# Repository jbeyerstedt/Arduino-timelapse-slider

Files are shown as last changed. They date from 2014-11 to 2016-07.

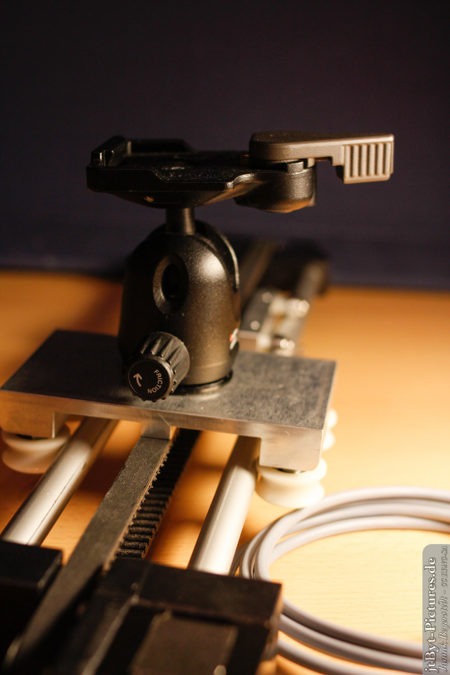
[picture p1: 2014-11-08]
additional files/Slider_Bilder-008.JPG

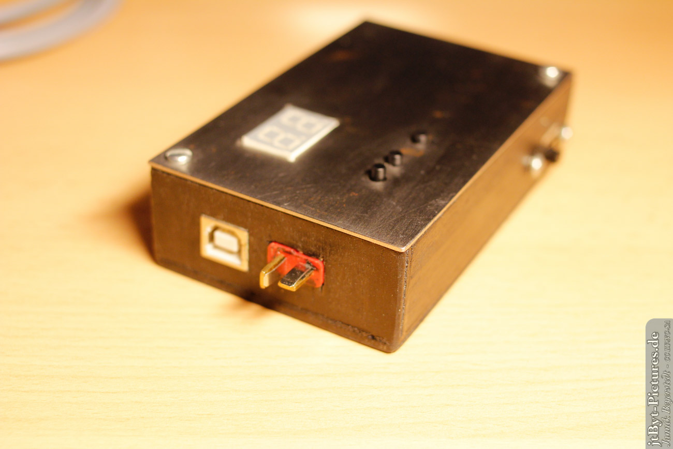
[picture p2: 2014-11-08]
additional files/Slider_Bilder-011.JPG

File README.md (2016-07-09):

# Arduino - timelapse-slider
by Jannik Beyerstedt from Hamburg, Germany  
[jannikbeyerstedt.de](http://jannikbeyerstedt.de) | [Github](https://github.com/jbeyerstedt)  
**license:** GNU GPL v3

## Software Documentation
This readme contains the introduction of the project, changelog and the **user manual** for the code/ software. Check also the "hardware_readme.md" and "electronics_readme.md".

## Introduction
I'm beginning shooting time lapses with my DSLR camera and wanted to have a slider for more interesting camera movements in my time lapses. So I began to write some code for the Arduino UNO board to control a stepper motor and the trigger of my camera.
To control this little thing I will use three buttons and two 7 digit displays.

You can find photos I made and in the future also videos on my website [jannikbeyerstedt.de](https://jannikbeyerstedt.de/fotografie).

## User Manual  
#### general information
1. the total slide time influences the sliding speed!

#### step by step guide
1. switch on power
2. The software initializes
	1. give it the starting point (left or right)
3. choose mode: interval trigger (**in**terval), timelapse slide (**sl**ide), movie (**co**ntinuous)
4. manual control (all modes the same)
	1. move carriage with plus and minus buttons
5. at interval trigger mode (it´s an interval trigger only)
	1. set trigger interval
	2. set direction
	3. push enter to begin
	4. end with enter -> back to step 4
6. at timelapse slide mode (interval trigger and carriage movement)
	1. set total slide time
	2. set direction
	3. set trigger interval
	4. push enter to begin
	5. it´ll end if time is elapsed or endstop hit -> back to step 4
	6. or abort by clicking enter -> back to step 4
7. at movie mode (no trigger, only carriage movement)
	1. set total movement time
	2. set direction
	3. push enter to begin
	4. it´ll end if time is elapsed or endstop hit -> back to step 4
	5. or abort by clicking enter -> back to step 4
8. change mode by reconnecting power or resetting the arduino

Symbols:

- In -> interval mode
- SL -> slider mode
- co -> movie mode (continuous)
- dr -> set total time (drive)
- In -> set trigger interval
- ┌ ┐ -> moving carriage
- \[ \] -> triggering camera
- – –  -> waiting for next triggering (interval trigger mode only)
- . -> idle/ manual drive possible

## Setup Manual
This will explain the options that can be set in the config.h file. But it´s quite well commented in the file itself as well.  
more follows soon / mehr folgt bald  

## what should the software do?
#### in general
* input values: time to slide the whole slider, slide direction, trigger interval
* have a stop button to escape the slide
* trigger the camera
* stop the slide at triggering the camera
* tree buttons as inputs (plus, minus, enter)
* drive two 8-bit shift registers for the displays
* drive a stepper motor (via stepper motor driver IC)

#### additional in version 1.0
* movie mode with constant velocity
* (more or less) smart symbols on the display indicating the direction, current mode and errors

#### additional in version 2.0
* INFO: movie and interval mode are disabeled until ready in v2.1
* coded as finite state machine
* 3 modes for timelapse, timelapse with slider, movie
* virtual endstops
* steps are done in the background
	* faster stepping possible
	* more responsive exit from slide
* set initial carriage position
* remember last settings (start at last entered number for slideTime, etc.)
* better virtual endstop methods
* some extensive serial prints can be disabled
* functionality for pure interval triggering added 

#### additional in version 2.1
* functionality for movie mode

## Changelog
* 1.0.1:
	* setSlideTime=0 will get an division through 0 in the calculation which causes malfunction (because stepsPerInterval will be 0)
	* corrected the calculation of the stepsPerInterval at high speed / setSlideTime < 3 / calculated stepsPerSecond < than the highest possible speed
* 1.0.2:  
	* little modification at big slide times
* 2.0 beta1 :
	* INFO: movie and interval mode are disabeled until ready in v2.1
	* all new rewritten version. New software concept and it´s C++ now.
	* 3 modes for timelapse, timelapse with slider, movie
	* classes for:
		* the slider (carriage)
		* the stepper motort
		* the buttons
	* display.h restructured and enhanced:
		* "dynamic" calcualtion of the symbols
		* new function for symbols only
		* number function does ONLY numbers now
		* number function can do negative numbers up to -9
	* enter start position (for virtual endstops)
	* move carriage with plus and minus buttons (for position counting)
* 2.0.1:
	* remember last settings (start at last entered number for slideTime, etc.)
	* better virtual endstop methods
	* some extensive serial prints can be disabled
	* functionality for pure interval triggering added
	* several bugfixes
* 2.1.0:
	* movie mode added
	
* TODO:
	* add a state machine documentation

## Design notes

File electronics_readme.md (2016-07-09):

# Arduino - timelapse-slider
by Jannik Beyerstedt from Hamburg, Germany  
[jannikbeyerstedt.de](http://jannikbeyerstedt.de) | [Github](https://github.com/jbeyerstedt)  
**license:** GNU GPL v3

## Electronics Documentation
This document describes the electronics part of the Arduino timelapse slider, but it will not be a complete instuction to rebuild everything I made. It´s more like all the parts you´ll need to build it, but there is enough you must do by yourself. I can´t explain every wire I used.  
Kepp in mind, that your camera may be triggered in a different way. Canon DSLRs are easy. You only must connect two pins of the remote connector. Some cameras are using different resistors to detect focus and trigger. Please ask google to find out more about your camera.

## parts I used:

amount | description  
--	| ---  
1	| Arduino Uno Rev3
1	| A4988 Stepper Motor Driver Carrier
2	| 8 bit shift registers
2	| 7 segment display (+ resistors)
1	| miniature relais (to trigger my Canon DSLR)
3	| miniature buttons
1	| T-connector (used at LiPo-batteries) for power supply

*	dot matrix circuit boards
*	pins to connect to the arduino
*	DIN-connectors for the wires to camera and motor
*	jumpers for different modes of the stepper motor driver
*	small wires with different colors to connect everything

**weblinks**

*	stepper motor driver: [http://www.exp-tech.de/Shields/A4988-Stepper-Motor-Driver-Carrier.html]()
*	stepper motor [http://www.exp-tech.de/Servos-und-Motoren/Stepper-Motor-Bipolar-200-Steps-Rev-35x36mm-2-7V-1000mA.html]()

## installation notes :
##### english:
###### display

*	you can drive one seven-segment-display each with one 8-bit shift register and you can connect two shift registers at one output of your arduino (but you will need tree pins for clock, latch and data)
*	connect each output of your shift register to one segment of the display with an restistor between them. Keep in mind, whether the display is collected kathode or anode and whether you can get positive or negative voltage from your shift register.
*	driving a shift register with an arduino is explained at the arduino website.
*	If you use my code copy and paste, than you have to check whether everything is connected to the same pin I used. Otherwise you must change the constants at the beginning of the code.

###### stepper motor

*	connect the stepper motor driver your arduino, an power supply and your stepper motor. Do never switch the driver on without an stepper motor (see manual of the driver).
*	read the manual and try the driver with a code snippet. If that works, you can put that code in your project.
*	If you use my code copy and paste, than you have to check whether everything is connected to the same pin I used. Otherwise you must change the constants at the beginning of the code.

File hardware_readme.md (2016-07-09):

# Arduino-Timelapse-Slider
# Arduino - timelapse-slider
by Jannik Beyerstedt from Hamburg, Germany  
[jannikbeyerstedt.de](http://jannikbeyerstedt.de) | [Github](https://github.com/jbeyerstedt)  
**license:** GNU GPL v3

## Hardware Documentation 
This is the documentation for the technical drawings and all the hardware.
all the technical drawings are specific to the parts I used. If you use other parts, some measurements must be changed.  

## basic Measurements

* distance between the tubes (inner edges): 45 mm
* tubes diameter: 12 mm
* bearings: 10mm x 4 mm

## parts I used

amount | description  
--	| ---  
12	| ball bearings MR 104 ZZ / 4 x 10 x 4 mm  
8	| zylindrical head screws M4x15  
4	| zylindrical head screws M4x20  
24	| nuts M4 (8 as distance roll, 16 as counter nut and for the correct distance)  
4	| rope reel with ball bearings (detailed information see weblink section) <br> outer diameter 24 mm, inner diameter 20 mm, height 11 mm  
4	| screws M5x15  
4	| nuts M5 (as counter nut and distance roll)  
1	| M5 screw and washer to fasten the quick release plate
1	| manfrotto 200PL quick release plate
1	| manfrotto ball head (using the 1/4 zoll screw of the QR-plate to fasten it)
1 m | toothed belt 5M-9 
2 	| toothed disk (gear) 12-5M-9 
4	| tiny M3 screws to secure the belt
1	| stepper motor (bipolar, 2.7V, 1000mA) by pololu

*	small screws to fasten the stepper motor

**weblinks**  

*	rope reel: [http://jost-technik.de/Klappensteller/Zubehoer---Sonstiges/Umlenkrolle-fuer-Huehnerklappe.html]()
*	ball brearings from ebay
*	toothed belt and disk: [https://zahnriemen24.de]()
*	stepper motor [http://www.exp-tech.de/Servos-und-Motoren/Stepper-Motor-Bipolar-200-Steps-Rev-35x36mm-2-7V-1000mA.html]()

## installation notes:
##### english:
###### tubes, tube support and stepper motor
*	build one tube support, that holds the two tubes and a gear for the belt
*	build another tube support, that can hold the stepper motor with the other gear on it.

###### inner sledge
*	the inner sledge uses the 10 mm bearings to be held in position. On every side (left and right) are 2 bearings at the top, 2 at the bottom and two on the inner side. All of them are on M4-Screws.
* 	the inner bearings have a nut on top and bottom as distance tubes, you can also use 3 mm thick tubes instead. The screw of these bearings is also used to hold the tree parts of the inner sledge together. They must be at least 15 mm long
* 	the outer bearings will be placed on the shorter M4 screws with two nut (each 3 mm) to hold them in place and keep them at the correct distance from the sledge.

###### outer sledge
*   put the rope reel on the M5 screw and secure with one nut. Screw it carefully to the aluminium base AND put it on the rails (tubes).

###### toothed belt
*	cut the belt in two pieces, drill a hole for the M3 screws betwen the tooths to one side of each belt
*	hold the belt on the slider to get the correct legth and mark the position for the screw. Kepp in mind, that the two belts will have different lenghts.
*	drill the other two holes
*	screw the belt to your slider

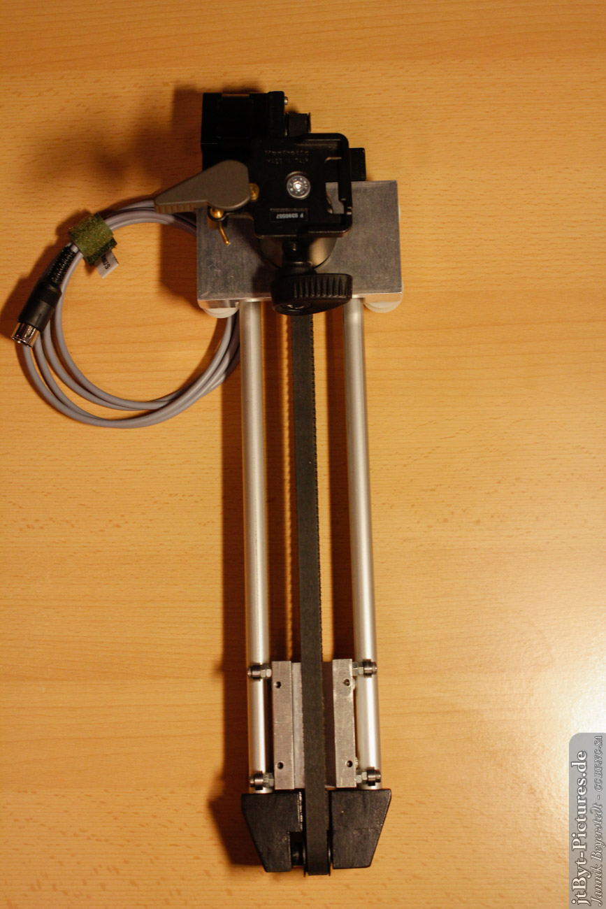
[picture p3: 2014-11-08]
additional files/Slider_Bilder-006.JPG

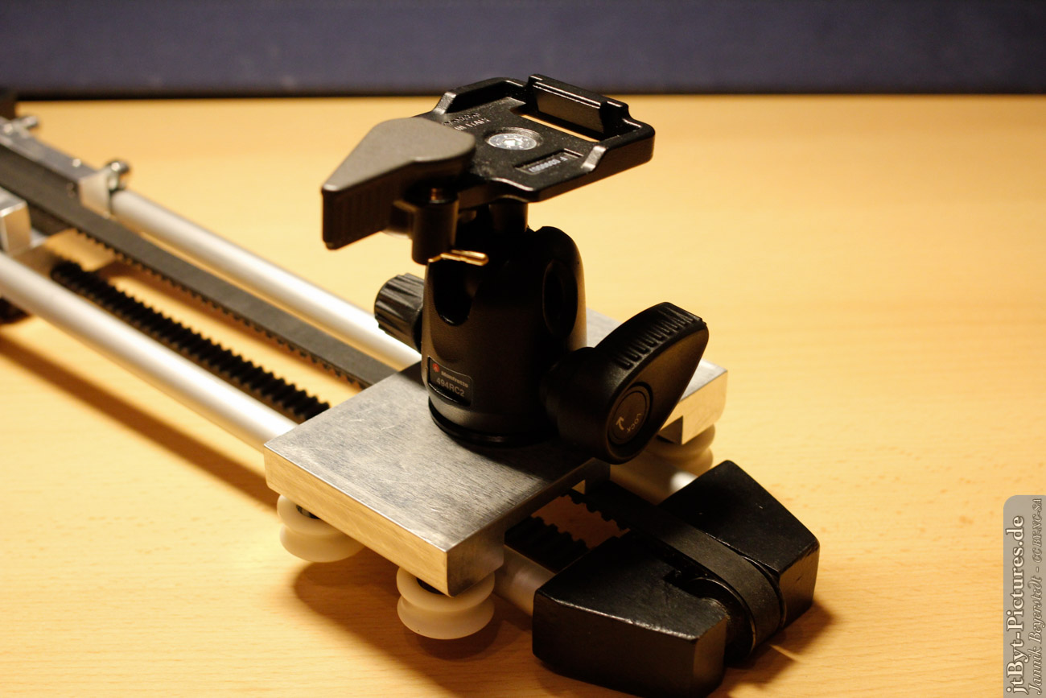
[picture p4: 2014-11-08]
additional files/Slider_Bilder-005.JPG

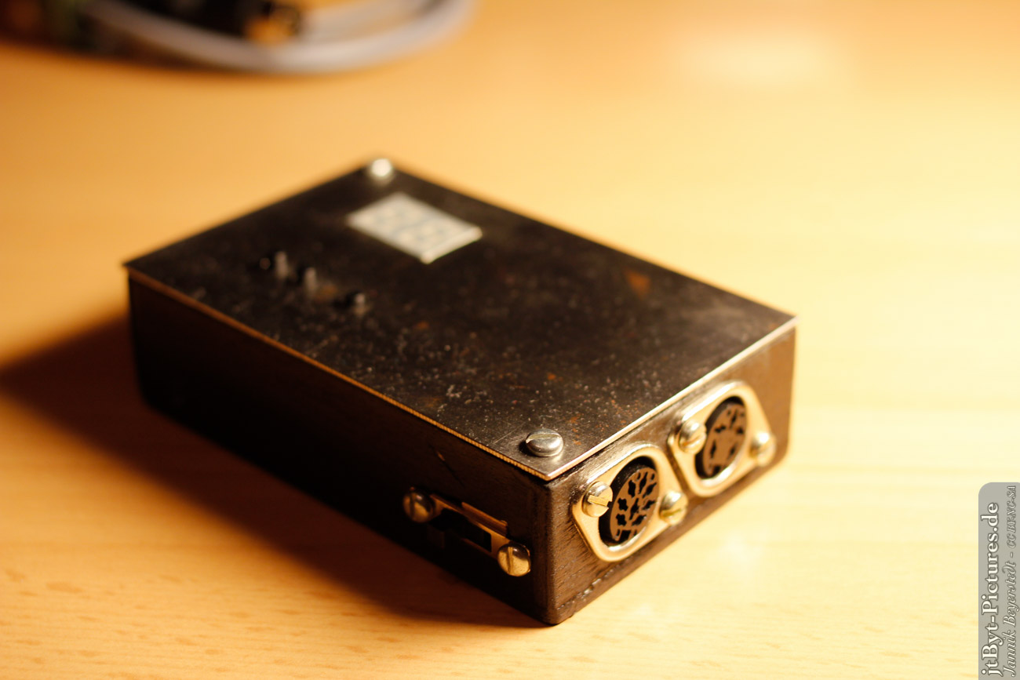
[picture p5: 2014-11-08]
additional files/Slider_Bilder-010.JPG

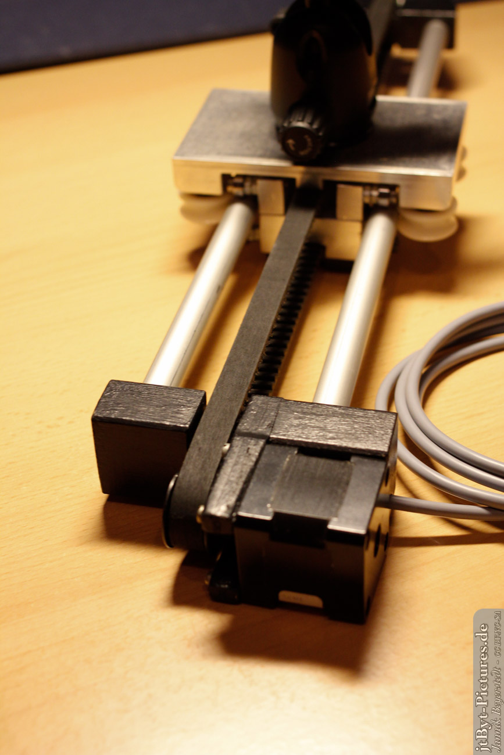
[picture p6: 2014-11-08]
additional files/Slider_Bilder-003.JPG

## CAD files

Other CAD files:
additional files/ArduinoSlider-Schlitten_Innen.dwg

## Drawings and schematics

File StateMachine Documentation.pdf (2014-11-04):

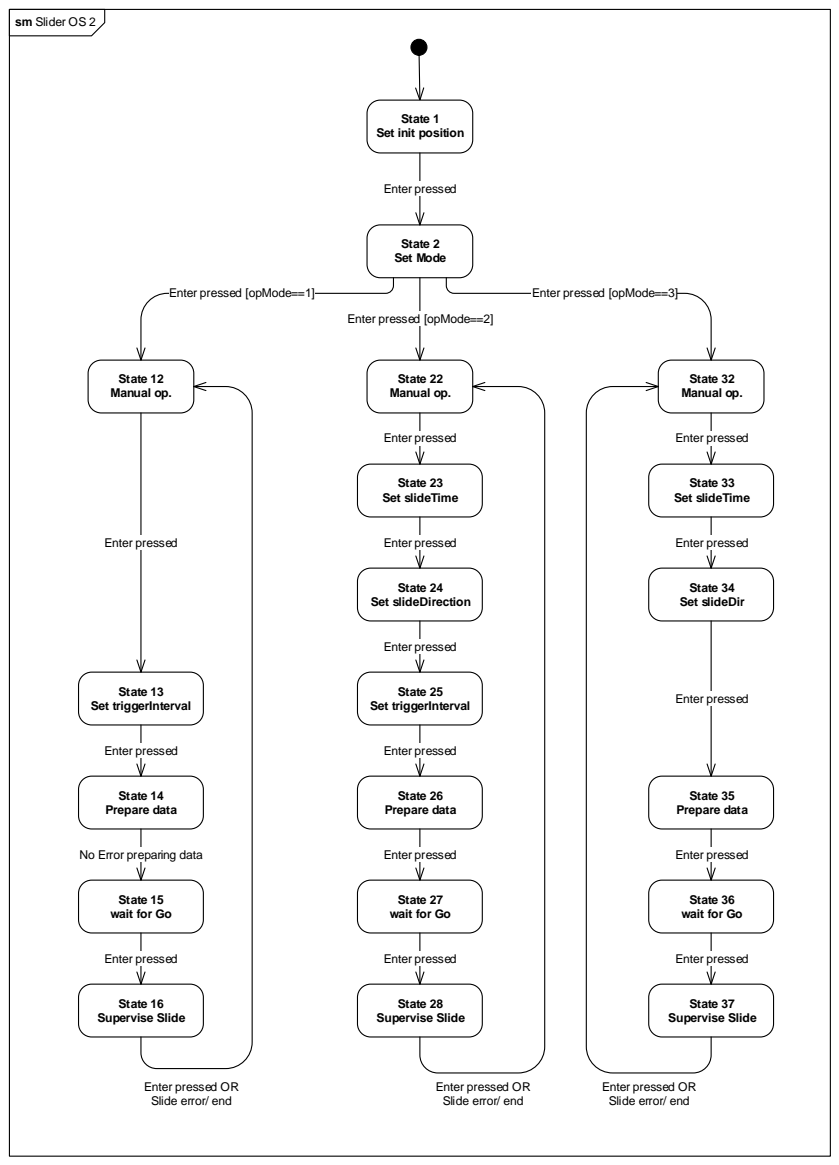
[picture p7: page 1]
State 12 Manual op.; State 22 Manual op.; State 32 Manual op.; State 2 Set Mode; Enter pressed; [opMode==2]; State 13 Set triggerInterval; State 23 Set slideTime; State 33 Set slideTime; State 24 Set slideDirection; State 34 Set slideDir; State 25 Set triggerInterval; State 14 Prepare data; State 35 Prepare data; State 26 Prepare data; No Error preparing data; State 16 Supervise Slide; State 28 Supervise Slide; State 37 Supervise Slide

sm Slider OS 2

State 1
Set init position

Enter pressed [opMode==1]

Enter pressed [opMode==3]

State 15
wait for Go

State 27

State 36

Enter pressed OR
Slide error/ end

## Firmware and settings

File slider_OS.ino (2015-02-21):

/*
 * project: slider OS 2
 * for controlling a timelapse slider and triggering the Camera
 * with an arduino, 3 buttons, 2 7-segment-displays, stepper driver
 *
 * for debouncing the buttons the Bounce2 library is used. Download it here:
 * https://github.com/thomasfredericks/Bounce-Arduino-Wiring
 * 
 * copyright: Jannik Beyerstedt | http://jannikbeyerstedt.de | code@jannikbeyerstedt.de
 * license: http://www.gnu.org/licenses/gpl-3.0.txt GPLv3 License
 *
 * version 2.1.1 (08.11.2014)
 * changelog: see readme.md
 */


#include <Bounce2.h>

#include "config.h"
#include "button.h"
#include "display.h"
#include "my_classes.h"
#include "slow_impulses.h"


int currentState = -1; 
int opMode  = 0;       // operation mode - 1: IN - 2: SL - 3: CO

int choosenNumber = 0;
boolean slideError = false;
int buttonsHelper = 0; // variable to temporarly store button return values
int buttonsLastVal = 0;

int slideTime = 1;
int slideDirection = 0; // 1 = right, 0 = left
int triggerInterval = 0;



ButtonPair buttons (buttonPlusPin, buttonMinusPin);
//Button buttonEnter (buttonEnterPin); // for a normally working button
Button2 buttonEnter (buttonEnterPin); // special for my broken button

SlowImpulses stepper;

Slider mySlider(&stepper);



void setup() {
  pinMode(ledPin, OUTPUT);
  pinMode(shiftLatch, OUTPUT);
  pinMode(shiftClock, OUTPUT);
  pinMode(shiftData, OUTPUT);
  
  pinMode(buttonPlusPin, INPUT);
  pinMode(buttonMinusPin, INPUT);
  pinMode(buttonEnterPin, INPUT);
  
  pinMode(stepperStep, OUTPUT);
  pinMode(stepperDir, OUTPUT);
  pinMode(stepperSleep, OUTPUT);
  
  pinMode(trigger, OUTPUT);
  
  digitalWrite(stepperSleep, LOW); // set stepper driver to sleep
  
  stepper.init(stepperStep);
  
  #ifndef NO_SERIAL_COM
  Serial.begin(9600);
  #endif
}


void loop() {
  
  // read all buttons
  buttons.update();
  buttonEnter.update();
  
  
  // do something based on the case
  switch (currentState) {
    
    case 1:  // initialize carriage position
      
      buttons.setInterval(0,2);
      buttonsHelper = buttons.getValue();  
      switch (buttonsHelper) {
        case 0: // left
          displaySymbol(initLeft);
          mySlider.initCarriagePosition(0);
          break;
        case 2: // right
          displaySymbol(initRigt);
          mySlider.initCarriagePosition(maxSteps);
          break;
        default:
          displaySymbol(initPos);
          break;
      }
      
      if (buttonEnter.triggered() ) {
        Serial.print("initial position: "); Serial.println(buttonsHelper);
        
        currentState = 2;
        #ifdef INFO_COM
        Serial.println("--switch to state 2");
        #endif
      }
      
      break;
    
    case 2:  // initialization / set mode
      buttons.setInterval(0,3);
      opMode = buttons.getValue();
      switch (opMode) {
        case 1: // IN
          displaySymbol(modeIn);
          break;
        case 2: // SL
          displaySymbol(modeSl);
          break;
        case 3: // CO
          displaySymbol(modeCo);
          break;
        default:
          displaySymbol(waitInput);
          break;
      }
      
      if (buttonEnter.triggered() ) {
        Serial.print("mode: "); Serial.println(opMode);
        switch (opMode) {
          case 1: // IN
            buttons.reset();
            buttons.setInterval(-maxSteps ,maxSteps, (1000/maxVelocity) ); // step interval = 1/maxVelocity in ms
            currentState = 12;
            #ifdef INFO_COM
            Serial.println("--switch to state 12");
            #endif
            break;
          case 2: // SL
            buttons.reset();
            buttons.setInterval(-maxSteps ,maxSteps, (1000/maxVelocity) ); // step interval = 1/maxVelocity in ms
            currentState = 22;
            #ifdef INFO_COM
            Serial.println("--switch to state 22");
            #endif
            break;
          case 3: // CO
            buttons.reset();
            buttons.setInterval(-maxSteps ,maxSteps, (1000/maxVelocity) ); // step interval = 1/maxVelocity in ms
            currentState = 32;
            #ifdef INFO_COM
            Serial.println("--switch to state 32");
            #endif
            break;
          default:
            displaySymbol(waitInput);
            Serial.println("ERROR: no mode set");
            break;
        }
      }
      
      break;
      
    case 12:  // manual operation / idle
    case 22:
    case 32:
      displaySymbol(waitIdle);
      
      buttonsHelper = buttons.getValue();
      
      digitalWrite(stepperSleep, HIGH);
      
      if (buttonsHelper > buttonsLastVal ) {        // right
        buttonsLastVal = buttonsHelper;
        mySlider.manualRight();
      }else if (buttonsHelper < buttonsLastVal ) {  // left
        buttonsLastVal = buttonsHelper;
        mySlider.manualLeft();
      }
      
      
      if (buttonEnter.triggered() ) {
        switch (opMode) {
          case 1: // IN
            buttons.setInterval(1,numberLimitTriggerTime);
            buttons.presetValue(triggerInterval); // preset last entered value
            
            displaySymbol(setInt); delay(500);
            currentState = 13;
            #ifdef INFO_COM
            Serial.println("--switch to state 13");
            #endif
            break;
          case 2: // SL
            buttons.setInterval(1,numberLimitSlideTime);
            buttons.presetValue(slideTime); // preset last entered value
            
            displaySymbol(setTime); delay(500);
            currentState = 23;
            #ifdef INFO_COM
            Serial.println("--switch to state 23");
            #endif
            break;
          case 3: // CO
            buttons.setInterval(1,numberLimitSlideTime);
            buttons.presetValue(slideTime); // preset last entered value
            
            displaySymbol(setTime); delay(500);
            currentState = 33;
            #ifdef INFO_COM
            Serial.println("--switch to state 33");
            #endif
            break;
          default:
            displaySymbol(waitInput);
            currentState = 0;
            Serial.println("ERROR: no mode set -> reset");
            break;
        }
      }
      break;  
    
    case 23:  // set total time
    case 33:
      slideTime = buttons.getValue();
      displayNumber(slideTime);
      
      if (buttonEnter.triggered() ) {
        Serial.print("slideTime: "); Serial.println(slideTime);
        switch (opMode) {
          case 2: // SL
            buttons.setInterval(0,1);
            buttons.presetValue(slideDirection); // preset last entered value
            currentState = 24;
            #ifdef INFO_COM
            Serial.println("--switch to state 24");
            #endif
            break;
          case 3: // CO
            buttons.setInterval(0,1);
            buttons.presetValue(slideDirection); // preset last entered value
            currentState = 34;
            #ifdef INFO_COM
            Serial.println("--switch to state 34");
            #endif
            break;
          default:
            displaySymbol(waitInput);
            currentState = 0;
            Serial.println("ERROR: no mode set -> reset");
            break;
        }
      }
      break;
    
    case 24:  // set carriage movement direction
    case 34:
      slideDirection = buttons.getValue();  
      if (slideDirection == 1) { // right
        displaySymbol(dirRigt);
      }else if (slideDirection == 0) { // left
        displaySymbol(dirLeft);
      }
      
      if (buttonEnter.triggered() ) {
        Serial.print("slideDirection: "); Serial.println(slideDirection);
        switch (opMode) {
          case 1: // IN
            buttons.reset();
            currentState = 15;
            #ifdef INFO_COM
            Serial.println("--switch to state 15");
            #endif
            break;
          case 2: // SL
            buttons.setInterval(1,numberLimitTriggerTime);
            buttons.presetValue(triggerInterval); // preset last entered value
            
            displaySymbol(setInt); delay(500);
            currentState = 25;
            #ifdef INFO_COM
            Serial.println("--switch to state 25");
            #endif
            break;
          case 3: // CO
            buttons.reset();
            currentState = 35;
            #ifdef INFO_COM
            Serial.println("--switch to state 35");
            #endif
            break;
          default:
            displaySymbol(waitInput);
            currentState = 0;
            Serial.println("ERROR: no mode set -> reset");
            break;
        }
      }
      break;
    
    case 13:  // set trigger interval
    case 25:
      triggerInterval = buttons.getValue();
      displayNumber(triggerInterval);
      
      if (buttonEnter.triggered() ) {
        Serial.print("triggerInterval: "); Serial.println(triggerInterval);
        switch (opMode) {
          case 1: // IN
            buttons.reset();
            currentState = 14;
            #ifdef INFO_COM
            Serial.println("--switch to state 14");
            #endif
            break;
          case 2: // SL
            buttons.reset();
            currentState = 26;
            #ifdef INFO_COM
            Serial.println("--switch to state 26");
            #endif
            break;
          default:
            displaySymbol(waitInput);
            currentState = 0;
            Serial.println("ERROR: no mode set -> reset");
            break;
        }
      }
      break;
    
    case 14:  // prepare data / set slide parameters
    case 26:
    case 35:
      #ifdef INFO_COM
      Serial.println("--data preparation");
      #endif
      displaySymbol(waitGo);
      
      switch (opMode) {
        case 1: // IN
          mySlider.setParameters(opMode, 0, triggerInterval, 0);
          
          buttons.reset();
          currentState = 15;
          #ifdef INFO_COM
          Serial.println("--switch to state 15");
          #endif
          break;
        case 2: // SL
          mySlider.setParameters(opMode, slideTime, triggerInterval, slideDirection);
          
          buttons.reset();
          currentState = 27;
          #ifdef INFO_COM
          Serial.println("--switch to state 27");
          #endif
          break;
        case 3: // CO
          mySlider.setParameters(opMode, slideTime, 0, slideDirection);
          
          buttons.reset();
          currentState = 36;
          #ifdef INFO_COM
          Serial.println("--switch to state 36");
          #endif
          break;
        default:
          displaySymbol(waitInput);
          currentState = 0;
          Serial.println("ERROR: no mode set -> reset");
          break;
      }
      break;
    
    case 15:  // wait for go
    case 27:
    case 36:
      
      if (buttonEnter.triggered() ) {
        switch (opMode) {
          case 1: // IN
            buttons.reset();
            mySlider.startSequence();
            currentState = 16;
            #ifdef INFO_COM
            Serial.println("--switch to state 16");
            #endif
            break;
          case 2: // SL
            buttons.reset();
            mySlider.startSequence();
            currentState = 28;
            #ifdef INFO_COM
            Serial.println("--switch to state 28");
            #endif
            break;
          case 3: // CO
            buttons.reset();
            mySlider.startSequence();
            currentState = 37;
            #ifdef INFO_COM
            Serial.println("--switch to state 37");
            #endif
            break;
          default:
            displaySymbol(waitInput);
            currentState = 0;
            Serial.println("ERROR: no mode set -> reset");
            break;
        }
      }
      break;
    
    case 16:  // supervise slide operation
    case 28:
    case 37:
                  
      if ( mySlider.update() ) {
        // normal operation
        slideError = false;
      }else {
        // virtual endstop hit
        slideError = true;
        displaySymbol(errorGen);
        delay(1000);
      }
      
      
      if (buttonEnter.triggered() || (slideError) ) {
        switch (opMode) {
          case 1: // IN
            mySlider.stopSequence();
            
            buttons.reset();
            buttons.setInterval(-maxSteps ,maxSteps, (1000/maxVelocity) ); // step interval = 1/maxVelocity in ms
            currentState = 12;
            #ifdef INFO_COM
            Serial.println("--switch to state 12");
            #endif
            break;
          case 2: // SL
            mySlider.stopSequence();
            
            buttons.reset();
            buttons.setInterval(-maxSteps ,maxSteps, (1000/maxVelocity) ); // step interval = 1/maxVelocity in ms
            currentState = 22;
            #ifdef INFO_COM
            Serial.println("--switch to state 22");
            #endif
            break;
          case 3: // CO
            mySlider.stopSequence();
            
            buttons.reset();
            buttons.setInterval(-maxSteps ,maxSteps, (1000/maxVelocity) ); // step interval = 1/maxVelocity in ms
            currentState = 22;
            #ifdef INFO_COM
            Serial.println("--switch to state 32");
            #endif
            break;
          default:
            displaySymbol(waitInput);
            currentState = 0;
            Serial.println("ERROR: no mode set -> reset");
            break;
        }
        
      }
      break;
    
    default:
      // initialise all systems
      // or something wrong happened
      Serial.println("--reset (default case)");
      currentState = 1;
      buttons.presetValue (1); // init position: display "initPos" first.
      
      break;
  } // end switch
  
  
} // end loop





// timer compare interrupt service routine
// must be in main file / can´t figure out how to do it in the impulse.h or impule.cpp
ISR(TIMER1_COMPA_vect)
{ 
  if (stepper.durationCount < stepper.durationCompare ) {
    stepper.durationCount++;
    digitalWrite(stepper.pinNo, digitalRead(stepper.pinNo) ^ 1);
  }else {
    stepper.durationStatus = false;
    stepper.stop();
  }
}

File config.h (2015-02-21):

/*
 * project: slider OS 2
 * file: config.h
 *
 * copyright: Jannik Beyerstedt | http://jannikbeyerstedt.de | code@jannikbeyerstedt.de
 * license: http://www.gnu.org/licenses/gpl-3.0.txt GPLv3 License
 *
 * version 2.1.1 (08.11.2014)
 */

/*
  configurations file
*/


#ifndef __config_h__
#define __config_h__
 
// basic config
// --------------------

// define input pins
#define trigger 2
//#define servoTilt 3

#define buttonPlusPin  A1
#define buttonMinusPin A2
#define buttonEnterPin A0

// define output pins
#define shiftLatch   12
#define shiftClock    9
#define shiftData     8
#define ledPin       13
#define stepperStep   6
#define stepperDir    7
#define stepperSleep  4

// set mechanical properties
const int triggerDuration = 500;   // how long should your camera be triggered (exposure time is still set in camera)
const int maxSteps        = 1740;  // amount of steps to slide the slider along {my calue for half step: 2200}
const int maxVelocity     = 50;    // maximum number of steps per second you stepper motor can perform
#define INVERT_STEPPER_DIR         // invert stepper direction, that it matches your buttons (right button, slide right)


// advanced config
// --------------------

// define the maximum number displayed
const int numberLimitSlideTime = 30;    // maximum time input to slide (in minutes)
const int numberLimitTriggerTime = 10;  // maximum trigger interval time (in seconds)

// define the number os milliseconds to retrigger a count-up if button is held down
const int fastCountInterval = 150;

//#define DEBUG_COM                 // enable detailed info (position values) (default: off)
//#define INFO_COM                  // enable info log (state changes) messages via serial 
//#define NO_SERIAL_COM             // disable all serial communication (default: off)

// debug config
// --------------------
const int debounceDelay = 20;
const int readThreshold = 900;


#endif

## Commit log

2013-06-08 various improvements
    changed symbols for indicating different states
    added the enter button as abort of the slide
2013-09-01 AutoCAD files of the inner slider sledge
    bad quality, i´ll do a better technical drawing of all machined parts
    in the future
    [ArduinoSlider-Schlitten_Innen.dwg]
2013-09-01 update to version 0.3
    now, that the pysical part of the slider is ready, I updated some
    values,
    added the trigger,
    corrected the slide direction
    added the calulation section
    [slider_OS.ino]
2013-09-01 new arduino sketch to test the setup without conversion
    like version 0.2
2013-09-01 update to 1.0.1 minor bugfixes - see new changelog
    fixed two bugs
    added changelog to the readme.md
    [slider_OS.ino]
2013-10-10 deleted AutoCAD files
    because they will not be completed. New drawings will follow soon.
    [ArduinoSlider-Schlitten_Innen.dwg]
2014-10-13 added another state for initialization of carriage
    changes for new Slider::setParameters
2014-10-13 experiments for driving stepper
    commit before changing to new branch, because it´s not working now.
    [my_classes.cpp]
2014-10-13 serious fix of problems with pointers
    pointer to the stepper instance was handled wrong
    [my_classes.cpp]
2014-10-13 init carriage position, housekeeping
    new state for initializing the carriage position
    plenty of housekeeping
2014-10-18 release version of buttons library
2014-10-19 v2.0 beta1
    new function for inverting stepper dir if necessary
    [config.h]
2014-10-21 little bugfix in manualLeft
    changed maximum frequency for manual operation to the maximum set in
    config.h
    [my_classes.cpp, slider_OS.ino]
2014-10-21 remember last set values
    therefore added ButtonPair::presetValue
2014-10-21 new positioning function for SL-mode
    + bugfix: forgot to make the changes of the last commit also on one
    other position
    [my_classes.cpp, slider_OS.ino]
2014-10-21 print some status info only for debug
2014-10-21 v2.0.1: functionality for interval trigger added
    + bugfixes
    + new error symbol
    + intervalTrigger class
    + some proper names
    [config.h, my_classes.cpp, slider_OS.ino]
2014-10-24 IntervalTrigger v2.0.2: bug at long execution times
    at long execution times there was an integer overflow in one
    calculation. Fixed by explicit conversion to long
    [my_classes.cpp]
2014-11-02 one state numbers fix
    and proper name for operation mode
    [slider_OS.ino]
2014-11-08 v2.1.1: new symbols added to UI + less info possible
    + I created some symbols for setting slide time and interval, but i
    forgot to implement them (Show the symbols for a short time before
    setting the value)
    + another level of info messages via Serial can be disabled (see
    config.h)
    [config.h, slider_OS.ino]
2014-11-08 Revert 16f6b82..ff59064
    This rolls back to commit 16f6b8262443ebfc880b34ca9ffc84aeaeb730ce.
    [config.h, slider_OS.ino]
2014-11-08 v2.1.1 new symbols added to UI + less info possible
    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
    [config.h, slider_OS.ino]
2015-07-19 fix: problems with long times
    [my_classes.cpp]
